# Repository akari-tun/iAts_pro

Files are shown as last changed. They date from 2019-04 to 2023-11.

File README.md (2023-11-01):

# iAts_pro(Antenna automatic tracking system pro)

## AAT test video
You can see the test video at [here](https://www.bilibili.com/video/av53142016).

## Development is on the way...

Not long ago, I created an automatic tracking system that supports bluetooth connection and parameter configuration based on the open source project [amv-open360tracker](https://github.com/raul-ortega/amv-open360tracker/) (You can find my project at [here](https://github.com/akari-tun/iAts)).

This project was built with Ateml 328p. As it is an 8-bit chip, its performance was low, so I couldn't implement more functions on it.Therefore, I came up with the idea of redeveloping it built on chips with higher performance.

Through the project of [RavenLRS](https://github.com/RavenLRS), I got to know a module espressif-ESP32 designed for IOT, which is integration bluetooth and wifi, and has 240mhz main frequency and 2m+ flash. And the official provides good SDK for development, which meets my needs very much. Therefore, I redeveloped the antenna automatic tracking system on this module.

After I graduating from college, I never use C language to develop any project, using C language development this project is a big challenge to me, I need to relearn C language feature, and the need to better understand how to use of Point. 

[RavenLRS](https://github.com/RavenLRS) project is built on ESP32 module, its also the realization of the function of some of its similar to some of my ideas, I learn by [RavenLRS](https://github.com/RavenLRS) project by learned a lot of of C language development experience, and use a lot of RavenLRS code to my project,Thanks to [RavenLRS](https://github.com/RavenLRS) author [fiam](https://github.com/fiam) open source for such an excellent project.

## How to Building iAts_pro
iAts_pro is built base on [esp-idf](https://github.com/espressif/esp-idf) v3.0 and has includes in path `/lib/esp-idf` as submodule, you need to install [Xtensa toolchanl](https://dl.espressif.com/dl/esp32_win32_msys2_environment_and_toolchain-20181001.zip) and set up the software environment follow the [ESP-IDF Programming Guide](https://docs.espressif.com/projects/esp-idf/en/v3.3/get-started/index.html).

Use command `git clone git@github.com:akari-tun/iAts_pro.git --recursive` to clone iAts_pro repository, `--recursive` option can clone all submoduls that includes, the submodul already points to the correct `Commit` from respository of `esp-idf` , do not need update it to lastest version.

Follow these command to build iAts_pro from your repository directory:

``` sh
cd iAts_pro
TARGET=esp32_iAts_pro_180 make
```

And you can add `PORT=<port>` and `flash` option to flash to your board like this:

``` sh
TARGET=esp32_iAts_pro_180 PORT=com1 make flash
```

## Companion App
I designed a android app for this project [Aircaft Viewer](https://github.com/akari-tun/iAts_pro/blob/master/tools).this app can be control aat to course the right direction and view the aircraft's location and some status infomation from the telemetry data.Its supported two protocol now.

## The Cases and STL file

[Body Build](https://github.com/akari-tun/iAts_pro/tree/master/doc/cases)

##### App Image

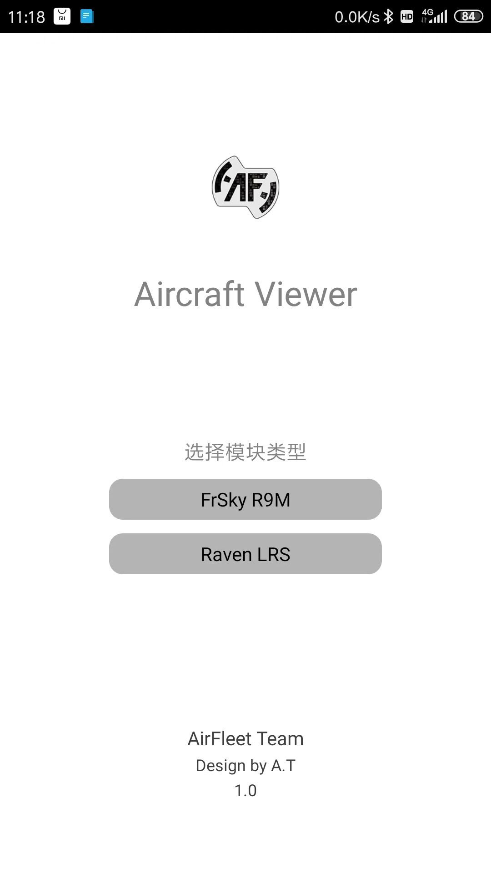
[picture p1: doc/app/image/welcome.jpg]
welcome


main page

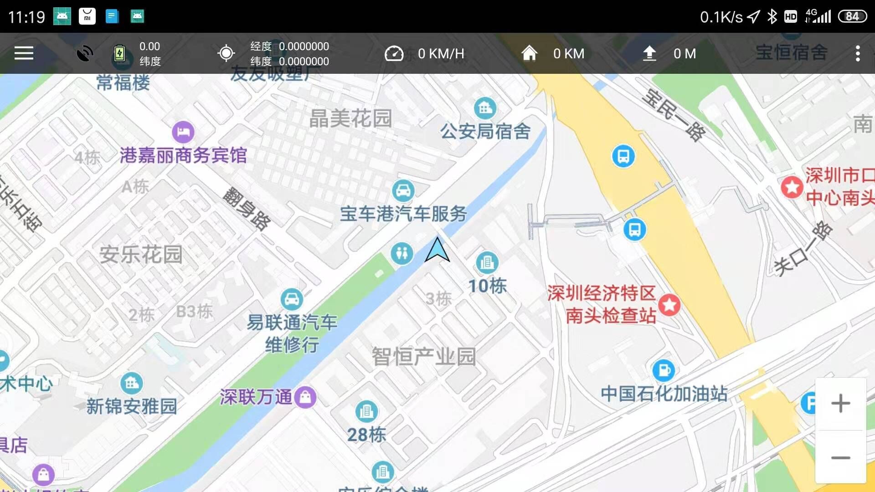
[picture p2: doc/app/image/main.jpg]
main

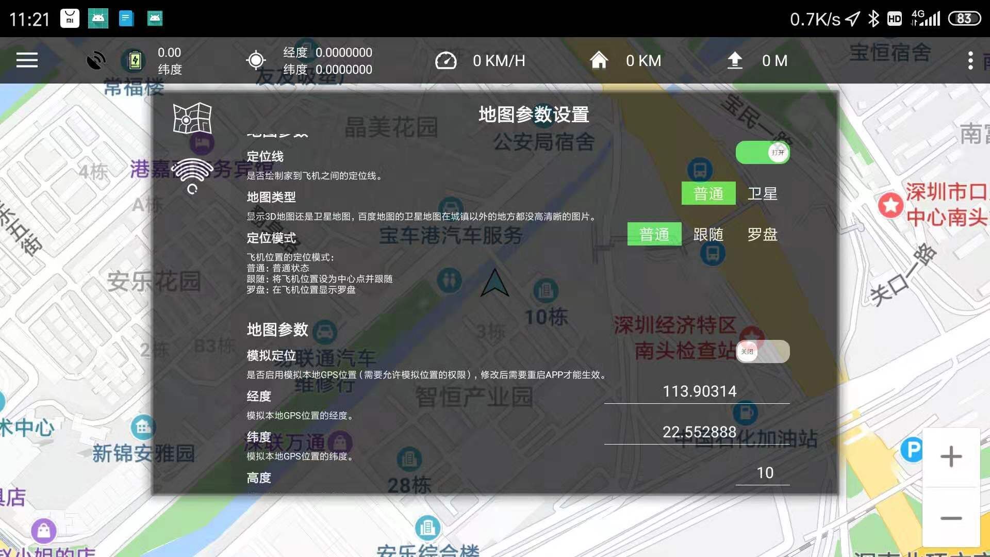
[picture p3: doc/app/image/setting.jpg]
setting


##### Smartport from R9M
Frsky R9m module can output Smartport, I diy a HC-05 module, It contains the inverter. So it's easy to plug to the R9m.

My app use classic bluetooth to connect HC-05 and get Smartport.

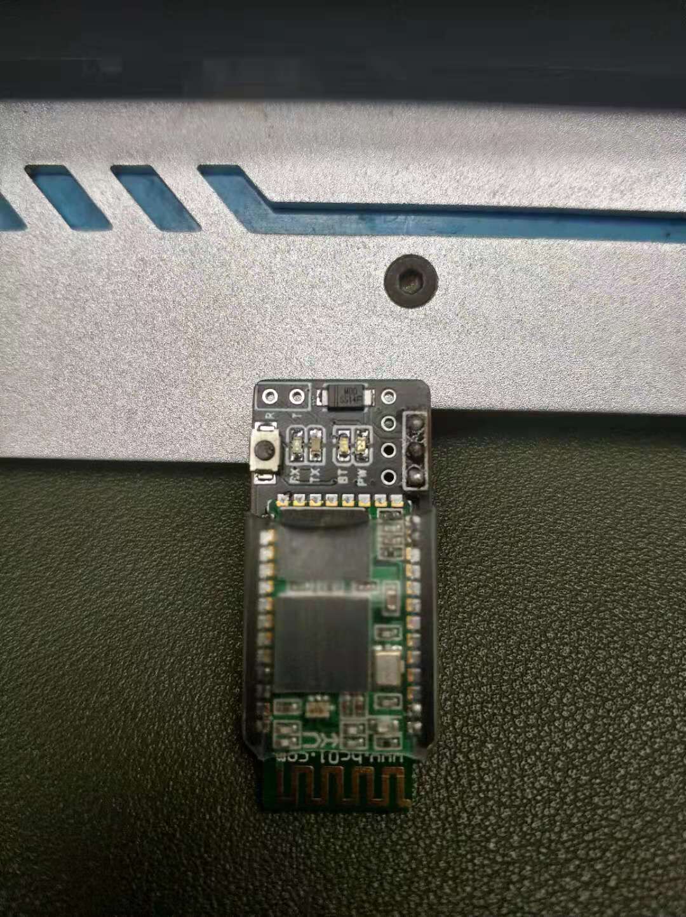
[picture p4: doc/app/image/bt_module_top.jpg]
bt_module_top

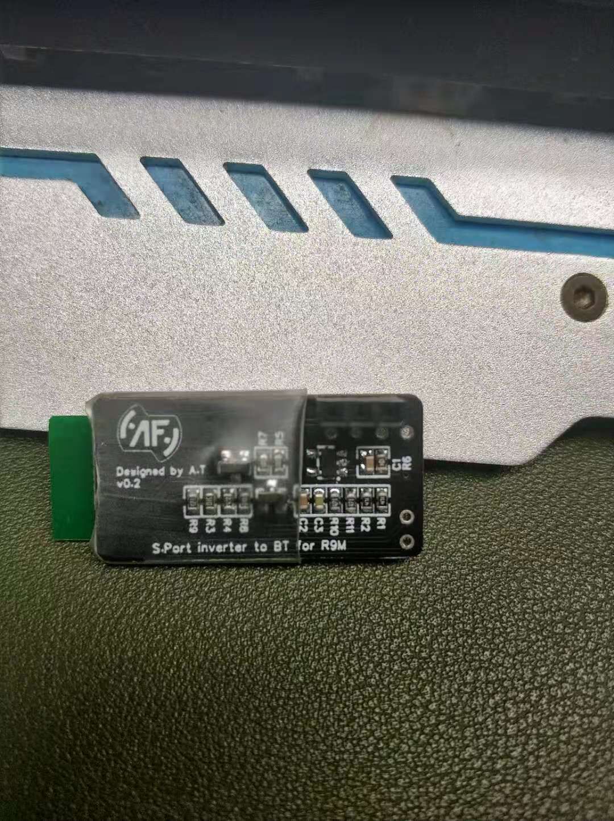
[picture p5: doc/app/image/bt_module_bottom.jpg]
bt_module_bottom


plugged to R9m

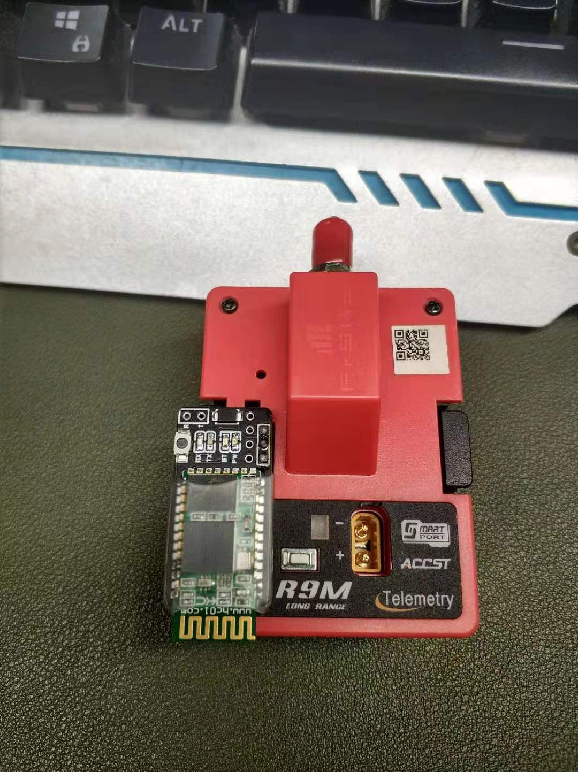
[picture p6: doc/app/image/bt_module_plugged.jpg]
bt_module_plugged


##### Raven LRS

[RavenLRS](https://github.com/RavenLRS) provides telemetry service for BLE's gatt server, but it don't provides notify.So I add the gatt server notify to RavenLRS,my app can use BLE notify get telemetry data.

You can find this module at here: [AF_TX_Lite](https://github.com/RavenLRS/raven-hardware/tree/AFelite)

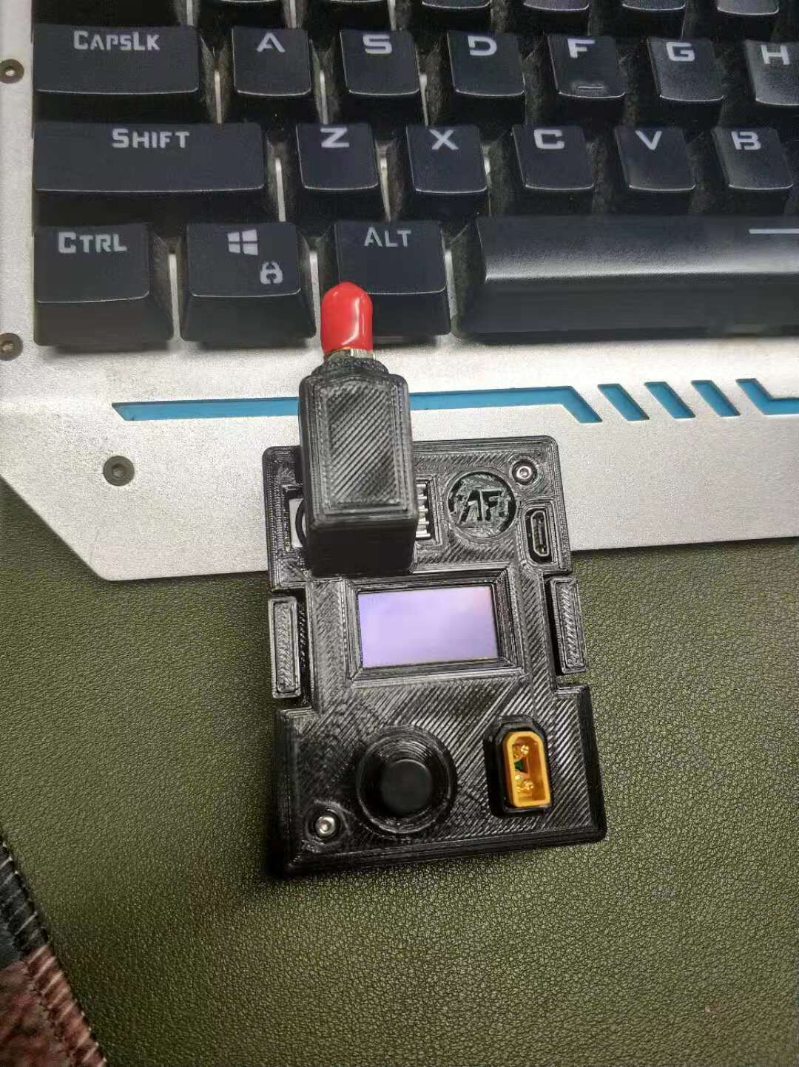
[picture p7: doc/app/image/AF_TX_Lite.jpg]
AF_TX_Lite


### PCB LAYOUT

#### PCB_LAYOUT_TOP
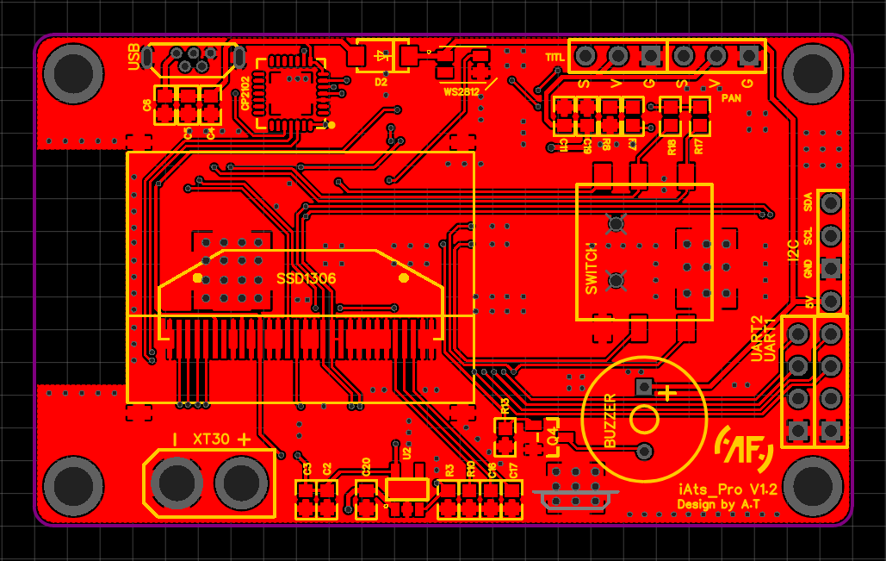
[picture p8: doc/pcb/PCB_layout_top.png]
PCB_LAYOUT_TOP


#### PCB_LAYOUT_BOTTOM
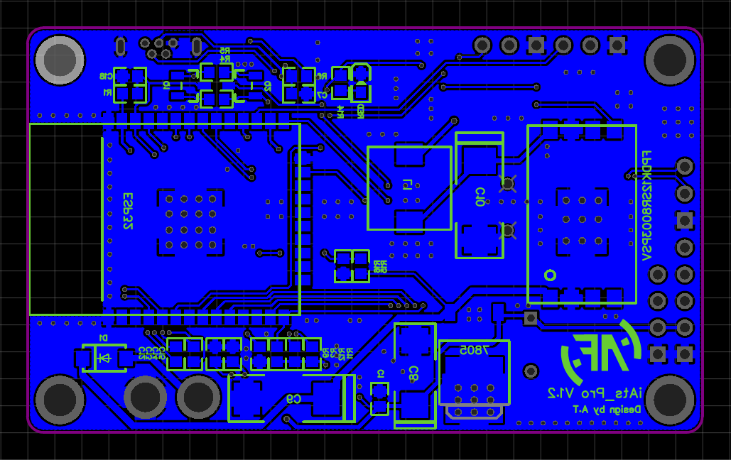
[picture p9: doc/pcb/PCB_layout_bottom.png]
PCB_LAYOUT_BOTTOM


### 3D PCB LAYOUT

#### 3D_PCB_LAYOUT_TOP
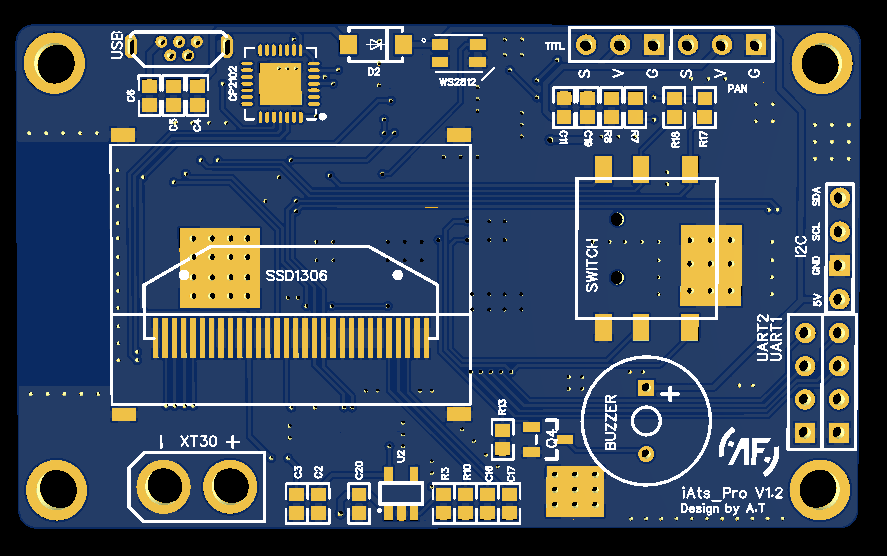
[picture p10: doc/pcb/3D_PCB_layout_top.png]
3D_PCB_LAYOUT_TOP


#### 3D_PCB_LAYOUT_BOTTOM
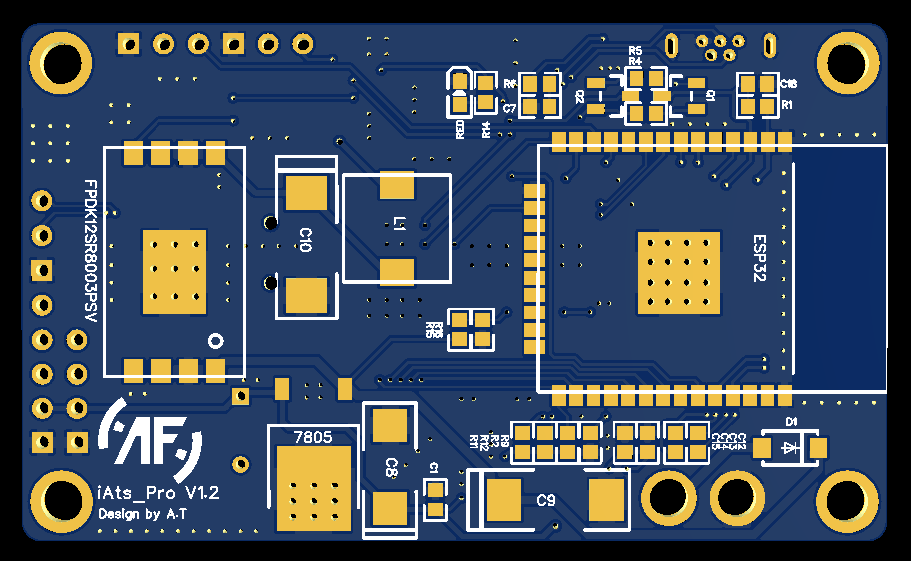
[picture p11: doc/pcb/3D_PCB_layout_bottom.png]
3D_PCB_LAYOUT_BOTTOM


### DESIGN IMAGE

#### 3D Printed
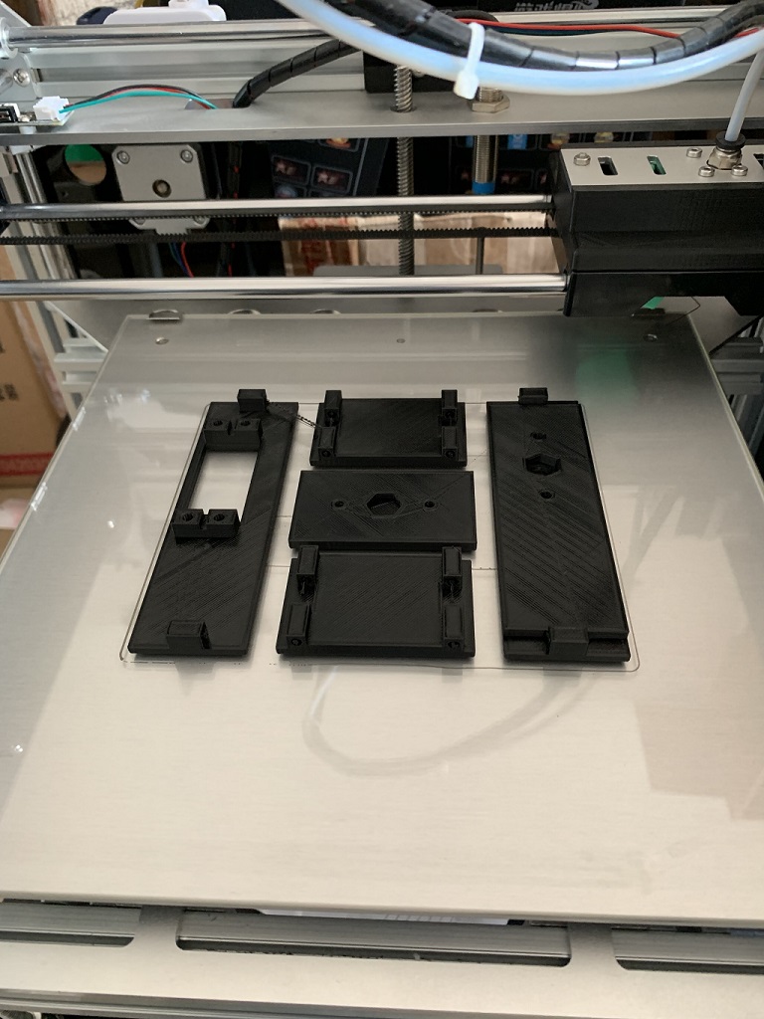
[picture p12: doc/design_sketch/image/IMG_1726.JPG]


#### Setup 1
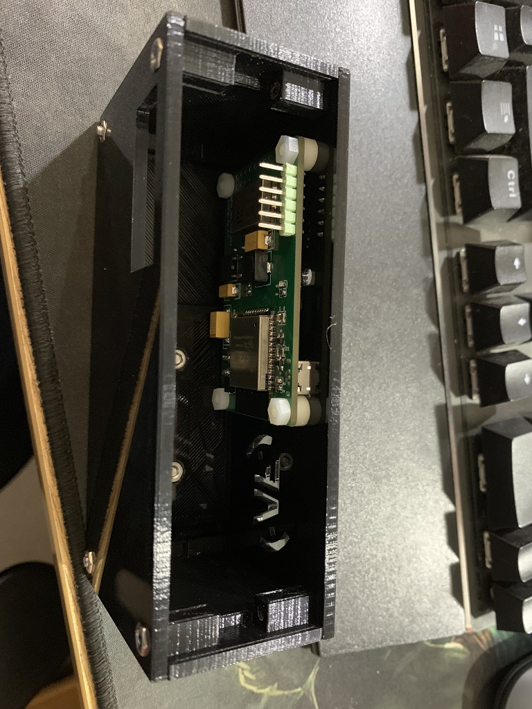
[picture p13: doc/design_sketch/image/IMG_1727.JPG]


#### Setup 2
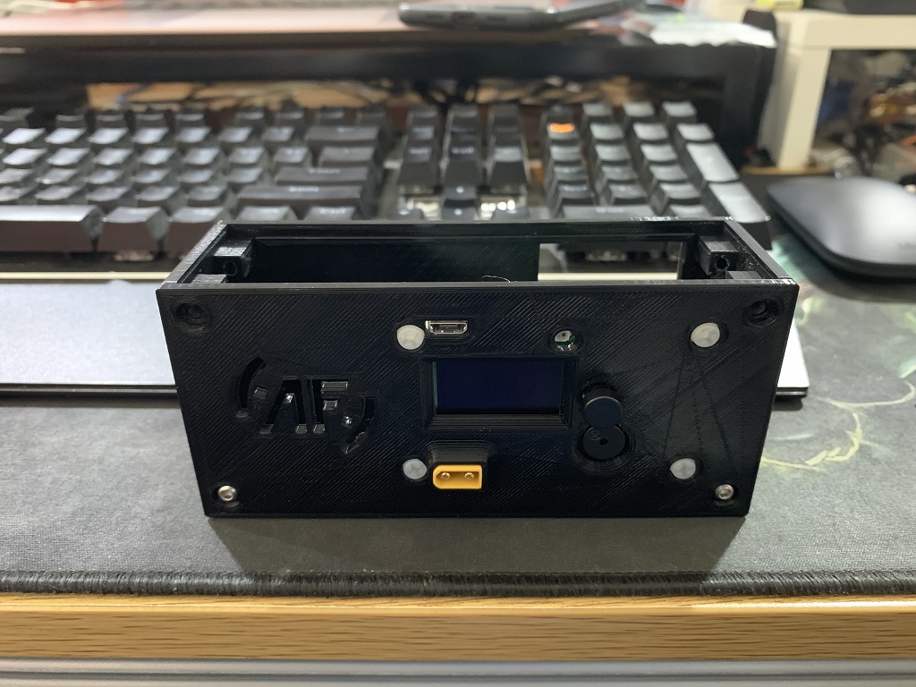
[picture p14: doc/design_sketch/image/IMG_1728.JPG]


#### Setup 3
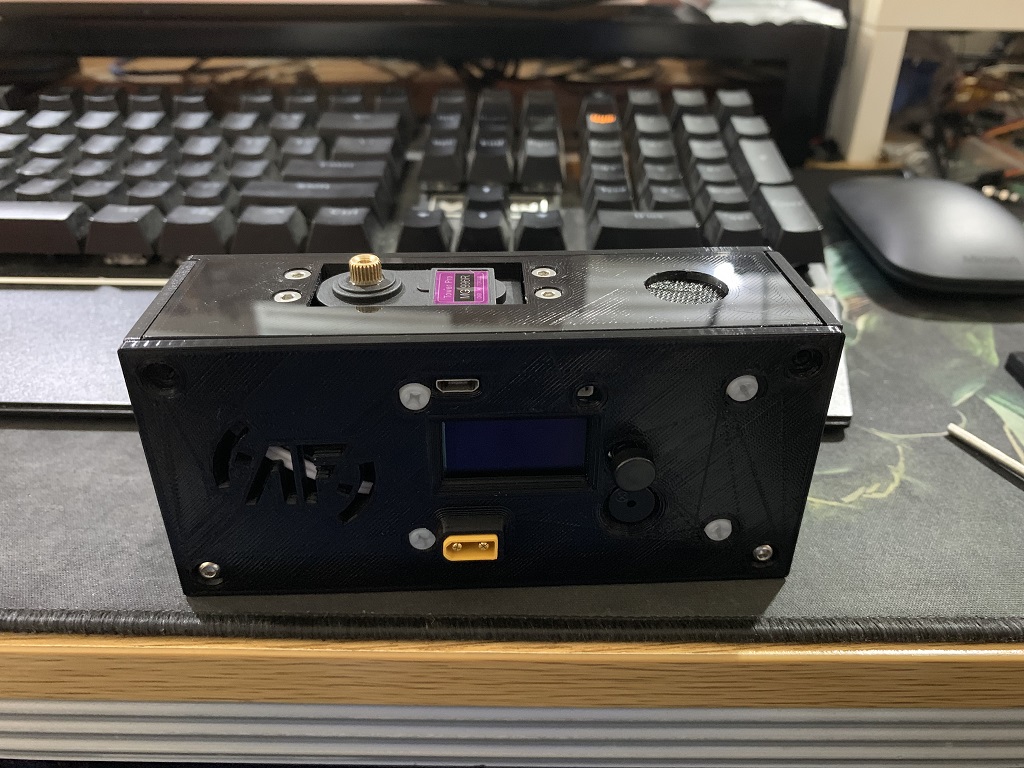
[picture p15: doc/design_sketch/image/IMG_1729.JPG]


#### Setup 4
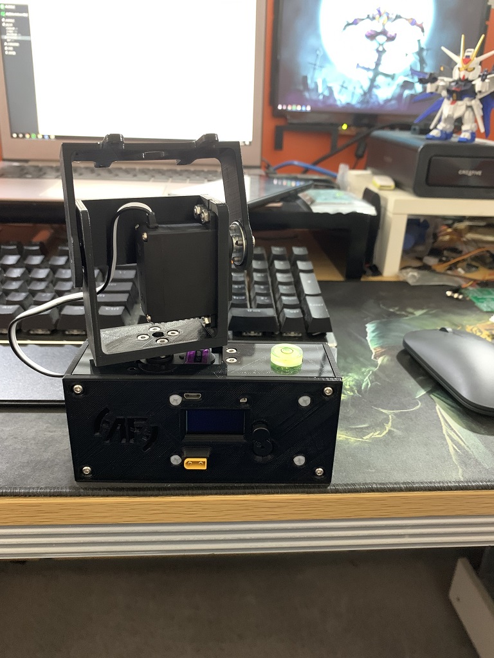
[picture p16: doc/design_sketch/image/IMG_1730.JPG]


#### Setup 5
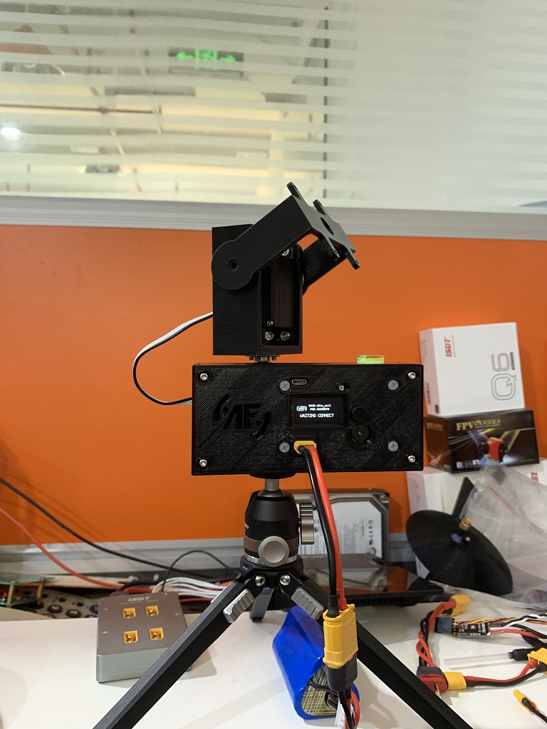
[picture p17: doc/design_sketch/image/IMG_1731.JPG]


#### Setup 6
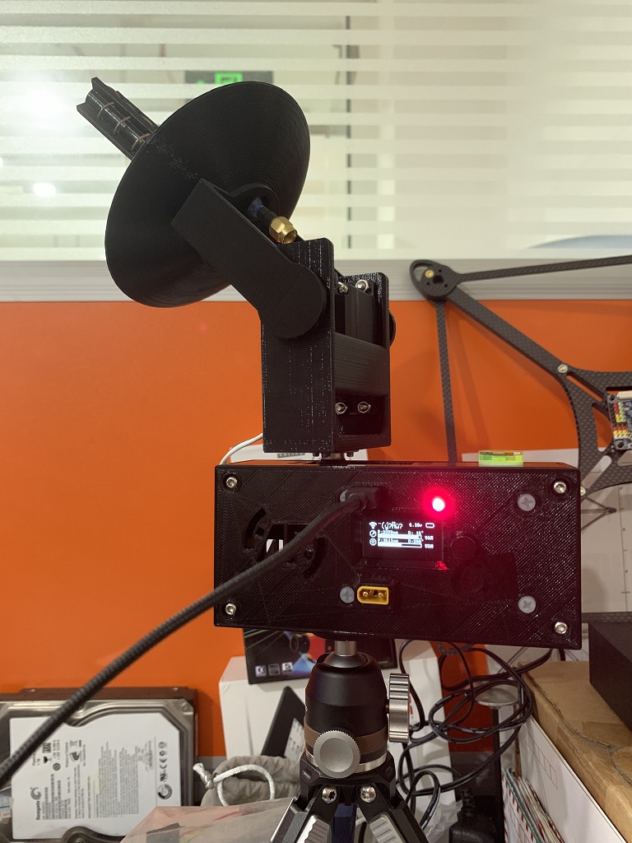
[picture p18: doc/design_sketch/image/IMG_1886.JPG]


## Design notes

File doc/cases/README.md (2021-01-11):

### Body
I provide STL files that can be sliced, and STP files that can be modified, so that you can modify the shell according to your own requirements.

### Print parameter
I use PLA filament to print this cases, 0.2mm resolution and 50% infill, at 1mm wall it has more strength, use 40mm/s speed for higher print quality.

### Attachment list
8  X M3 * 16 [screw](https://detail.tmall.com/item.htm?id=15880165683) for front and back panel  
4  X M3 * 12 [screw](https://detail.tmall.com/item.htm?id=15880165683) for pan servo  
2  X M3 * 10 [screw](https://detail.tmall.com/item.htm?id=15880165683) for 1/4 inch nut  
4  X M3 * 8  [screw](https://detail.tmall.com/item.htm?id=15880165683) for tilt servo  
10 X M3 [nut](https://detail.tmall.com/item.htm?id=20955552239&skuId=4319440520071) for servo  
1  X M3 * 10 [hand screw](https://detail.tmall.com/item.htm?id=17969634781&skuId=27553086583) for tilt stand  
8  X M3 * 6 [screw](https://detail.tmall.com/item.htm?id=15880165683) for steering wheel  
4  X M3 * 5 [nylon screw](https://detail.tmall.com/item.htm?id=17937568105&skuId=35998198392) for main board   
2  X 25T [steering wheel](https://item.taobao.com/item.htm?id=610941541573)  
1  X 1/4 inch [nut](https://detail.tmall.com/item.htm?id=22539384837&skuId=4297171597003)  
1  X 15 * 6 [level vial](https://item.taobao.com/item.htm?id=525788874394)  
1  X MF128zz [bearing](https://detail.tmall.com/item.htm?id=593627759602&skuId=4095252424985)  

#### Use Countersunk Screw

[Countersunk Screw](https://github.com/akari-tun/iAts_pro/tree/master/doc/cases/Countersunk%20Screw)

### Servo
I use the standard size of the servo, but the sizes of each servo different. I adjusted the design for sizes of the servo, and I recommend the use of this servo.  
[Pan servo](https://item.taobao.com/item.htm?id=581039145230&_u=b1i80m591e6) 180° 25kg digital servo  
[Tilt servo](https://item.taobao.com/item.htm?id=583942389297&_u=b1i80m530e0) 180° 12kg short digital servo

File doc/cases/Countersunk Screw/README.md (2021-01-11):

### Attachment list
8  X M3 * 16 [countersunk screw](https://detail.tmall.com/item.htm?id=19815788248&skuId=24958167102) for front and back panel  
4  X M3 * 12 [countersunk screw](https://detail.tmall.com/item.htm?id=19815788248&skuId=24958167101) for pan servo  
2  X M3 * 10 [countersunk screw](https://detail.tmall.com/item.htm?id=19815788248&skuId=24958167100) for 1/4 inch nut

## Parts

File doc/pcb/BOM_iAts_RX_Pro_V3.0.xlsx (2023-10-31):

iAts_Pro V3.0
元件 | 位置 | 规格 | 数量
电阻
47Ω | R8 | R0603 | 1
100Ω | R21 | R0603 | 1
470Ω | R20 | R0603 | 1
620Ω | R19,R18,R7 | R0603 | 3
1K | R25,R15 | R0603 | 2
4.7K | R11,R9,R29,R28,R12,R6 | R0603 | 6
5.76K | R24 | R0603 | 1
10K | R17,R16,R26,R27,R13,R14 | R0603 | 6
12K | R1,R5,R2,R4 | R0603 | 4
30.9K | R23 | R0603 | 1
100K | R22,R3 | R0603 | 2
910K | R10 | R0603 | 1
电容
1nF | C8 | C0603 | 1
100nF | C18,C4,C7,C5,C22,C11,C21 | C0603 | 7
1uF | C15,C10,C12,C2,C14,C1,C13 | C0603 | 7
2.2uF | C17 | C0603 | 1
4.7uF | C16 | C0603 | 1
10uF | C9,C3,C6 | C0603 | 3
22uF | C24,C23 | C0603 | 2
22uF | C27,C25,C19,C26,C20 | C0805 | 5
电感
4.7uH | L2 | IND-SMD_L4.0-W4.0 | 1
二极管
SS14 | D2 | SMA_L4.3-W2.6-LS5.2-RD | 1
SS34 | D1 | SMA_L4.4-W2.8-LS5.4-RD | 1
三极管
S8050 | Q4,Q3,Q2,Q1 | SOT-23-3_L3.0-W1.7-P0.95-LS2.9-BR | 4
LED
KT-0603R | G,B,R,Y | LED0603-R-RD | 4
WS2812B-3528 | WS2812 | LED-3528_4P | 1
IC
SX2106S6CTR | SX2106 | SOT-23-6_L2.9-W1.6-P0.95-LS2.8-BL | 1
SSD1306 | SSD1306 | SSD1306-30PIN_JX_REVERSE | 1
FPDK12SR8003PSV | FPDK12SR8003PSV | FPDK12SR8003PSV | 1
ESP-WROOM-32 | ESP32 | WIFIM-SMD_ESP-WROOM-32 | 1
CP2102-GMR | CP2102 | QFN-28_L5.0-W5.0-P0.50-BL-EP | 1
RT9013-33GB | U2 | SOT-23-5_L3.0-W1.7-P0.95-LS2.8-BL | 1
其他
Micro Usb 180 | USB | MICRO USB 180 | 1
ZL-DCY09605-2705P-5 | BUZZER | BUZ-TH_BD9.6-P5.00-D0.7-FD | 1
5Way Switch | SWITCH | 5WAY SWITCH | 1
XT30 | XT30 | XT30UPB_MY | 1

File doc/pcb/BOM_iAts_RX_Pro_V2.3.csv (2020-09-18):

ID | Name | Designator | Footprint | Quantity | Manufacturer Part | Manufacturer | Supplier | Supplier Part | LCSC Assembly
1 | WS2812B-3528 | WS2812 | LED-3528_4P | 1 | WS2812B-3528 | Worldsemi
2 | 4.7K | R12,R9,R29,R28,R11,R6 | R0603 | 6 | 0603WAF4701T5E | UniOhm | LCSC | C23162 | Yes
3 | 620 | R18,R19 | R0603 | 2 | 0603WAJ0621T5E | UniOhm | LCSC | C25251
4 | 100uF | C9 | CAP-SMD_L7.3-W4.3-R-RD | 1 | TAJE107K020RNJ | AVX | LCSC | C78063 | Yes
5 | 470uF | C10 | CAP-SMD_L7.3-W4.3-R-RD | 1 | TAJE477K010RNJ | AVX | LCSC | C7234 | Yes
6 | 10uF | C19,C6,C3 | C0603 | 3 | CL10A106KP8NNNC | SAMSUNG | LCSC | C19702 | Yes
7 | 4.7uF | C16 | C0603 | 1 | CL10A475KO8NNNC | SAMSUNG | LCSC | C19666 | Yes
8 | 30.9K | R23 | R0603 | 1 | 0603WAF3092T5E | UniOhm | LCSC | C23022 | Yes
9 | 3PIN_SERVO_2.54 | TITL,PAN | 3PIN_SERVO_2.54 | 2 | ?
10 | 100K | R3,R22 | R0603 | 2 | 0603WAF1003T5E | UniOhm | LCSC | C25803 | Yes
11 | 4.7uH | L2 | IND-SMD_L4.0-W4.0 | 1 | NR4018T4R7M | Taiyo Yuden | LCSC | C92936
12 | SS14 | D2 | SMA_L4.3-W2.6-LS5.2-RD | 1 | SS14 | STARSEA | LCSC | C84343 | Yes
13 | XT30_MY | XT30 | XT30UPB_MY | 1
14 | 5Way Switch | SWITCH | 5WAY SWITCH | 1 | TS-007 h:9 Five directions | ReliaPro | LCSC | C3679
15 | 2.2uF | C17 | C0603 | 1 | CL10A225KO8NNNC | SAMSUNG | LCSC | C23630 | Yes
16 | SX2106S6CTR | SX2106 | SOT-23-6_L2.9-W1.6-P0.95-LS2.8-BL | 1 | SX2106S6CTR | SX | LCSC | C78161 | Yes
17 | 5.76K | R24 | R0603 | 1 | 0603WAF5761T5E | UniOhm | LCSC | C23070 | Yes
18 | 100uF | C8 | CAP-SMD_L3.5-W2.8-R-RD | 1 | TCJB107M006R0070 | AVX | LCSC | C8026 | Yes
19 | 100nF | C18,C7,C4,C5 | C0603 | 4 | CC0603KRX7R9BB104 | YAGEO | LCSC | C14663 | Yes
20 | 620Ω | R7 | R0603 | 1 | 0603WAF6200T5E | UniOhm | LCSC | C23220 | Yes
21 | RT9013-33GB | U2 | SOT-23-5_L3.0-W1.7-P0.95-LS2.8-BL | 1 | RT9013-33GB | RICHTEK | LCSC | C47773 | Yes
22 | 100 | R21 | R0603 | 1 | 0603WAF1000T5E | UniOhm | LCSC | C22775 | Yes
23 | 4PIN | UART2,UART1 | 2.5-4PIN | 2 | ?
24 | 1K | R15,R25 | R0603 | 2 | 0603WAF1001T5E | UniOhm | LCSC | C21190 | Yes
25 | 1uF | C13,C14,C1,C15,C12,C2 | C0603 | 6 | CL10A105KB8NNNC | SAMSUNG | LCSC | C15849 | Yes
26 | KT-0603R | R,G,B,G2 | LED0603-R-RD | 4 | KT-0603R | KENTO | LCSC | C2286 | Yes
27 | 10K | R16,R17 | R0603 | 2 | TC0325F1002T5E | UniOhm | LCSC | C128781 | Yes
28 | CP2102-GMR | CP2102 | QFN-28_L5.0-W5.0-P0.50-BL-EP | 1 | CP2102-GMR | SILICON LABS | LCSC | C6568 | Yes
29 | SS34 | D1 | SMA_L4.4-W2.8-LS5.4-RD | 1 | SS34 | STARSEA | LCSC | C83961 | Yes
30 | S8050 | Q1,Q4,Q3,Q2 | SOT-23-3_L3.0-W1.7-P0.95-LS2.9-BR | 4 | S8050 | CJ | LCSC | C2146 | Yes
31 | 100nF | C11,C20,C21 | C0603 | 3 | CL10B104JB8NNNC | SAMSUNG | LCSC | C24452 | Yes
32 | 4PIN_I2C | I2C | 4PIN_I2C | 1 | ? |  |  | undefined
33 | ZL-DCY09605-2705P-5 | BUZZER | BUZ-TH_BD9.6-P5.00-D0.7-FD | 1 | ZL-DCY09605-2705P-5 | ZLFY | LCSC | C194534
34 | 470 | R20 | R0603 | 1 | 0603WAF4700T5E | UniOhm | LCSC | C23179 | Yes
35 | 910K | R10 | R0603 | 1 | RC0603FR-07910KL | YAGEO | LCSC | C137672
36 | 12K | R4,R5,R1,R2 | R0603 | 4 | 0603WAF1202T5E | UniOhm | LCSC | C22790 | Yes
37 | SSD1306 | SSD1306 | SSD1306-30PIN_JX_REVERSE | 1
38 | 33uH | L1 | IND-SMD_L7.8-W7.8 | 1 | SWRH0704B-330MT | Sunlord | LCSC | C127735
39 | 47Ω | R8 | R0603 | 1 | 0603WAF470JT5E | UniOhm | LCSC | C23182 | Yes
40 | 10 | R27,R26,R13,R14 | R0603 | 4 | 0603WAF100JT5E | UniOhm | LCSC | C22859 | Yes
41 | Micro Usb 180 | USB | MICRO USB 180 | 1
42 | ESP-WROOM-32 | ESP32 | WIFIM-SMD_ESP-WROOM-32 | 1 | ESP-WROOM-32 | ESPRESSIF | LCSC | C95209
43 | FPDK12SR8003PSV | FPDK12SR8003PSV | FPDK12SR8003PSV | 1 | FPDK12SR8003PSV |  | FDK | undefined
44 | 2PIN | UART0 | 2PIN | 1 | ?

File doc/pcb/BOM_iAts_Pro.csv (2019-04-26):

ID | Name | Designator | Footprint | Quantity | Manufacturer Part
1 | CP2102-GMR | CP2102 | QFN-28_5X5X05P | 1 | CP2102-GMR
2 | 100nF | C4,C5,C7,C18 | 0603' | 4 | CC0603KRX7R9BB104
3 | 10uF | C6,C19,C20,C3 | 0603' | 4 | CL10A106KP8NNNC
4 | 4.7K | R6,R11,R12,R17,R18,R9 | 0603' | 6 | 0603WAF4701T5E
5 | S8050 | Q1,Q2,Q4 | SOT-23(SOT-23-3) | 3 | S8050
6 | 12K | R4,R5,R1,R2 | 0603' | 4 | 0603WAF1202T5E
7 | Micro Usb 180 | USB | MICRO USB 180 | 1 | ?
8 | 470uF | C9,C10 | CASE-E_7343 | 2 | TAJE477K010RNJ
9 | SS34 | D1 | SMA(DO-214AC) | 1 | SS34
10 | FPDK12SR8003PSV | FPDK12SR8003PSV | FPDK12SR8003PSV | 1 | FPDK12SR8003PSV
11 | 620Ω | R7 | 0603' | 1 | 0603WAF6200T5E
12 | 47Ω | R8 | 0603' | 1 | 0603WAF470JT5E
13 | 33uH | L1 | 0704' | 1 | SWRH0704B-330MT
14 | 100nF | C11 | 0603' | 1 | CL10B104JB8NNNC
15 | SS14 | D2 | SMA(DO-214AC) | 1 | SS14
16 | 7805 | 7805 | TO252 | 1 | ?
17 | 100uF | C8 | CASE-C_6032 | 1 | TAJC107K016RNJ
18 | 10 | R15,R13 | 0603' | 2 | 0603WAF100JT5E
19 | 1K | R16 | 0603' | 1 | 0603WAF1001T5E
20 | XT30_MY | XT30 | XT30UPB_MY | 1 | ?
21 | ESP-WROOM-32 | ESP32 | ESP-WROOM-32 | 1 | ESP-WROOM-32
22 | WS2812B-3528 | WS2812 | LED-3528_4P | 1 | WS2812B-3528
23 | 4PIN_I2C | I2C | 4PIN_I2C | 1 | ?
24 | 4PIN | UART1,UART2 | 2.5-4PIN | 2 | ?
25 | 3PIN_SERVO_2.54 | TITL,PAN | 3PIN_SERVO_2.54 | 2 | ?
26 | ZL-DCY09605-2705P-5 | BUZZER | BUZZER-R9.6-2P-5.0PITCH | 1 | ZL-DCY09605-2705P-5
27 | 5Way Switch | SWITCH | 5WAY SWITCH | 1 | TS-007 h:9 Five directions
28 | 0.96-OLED-30Pin_JX | SSD1306 | SSD1306-30PIN_JX | 1 | 0.96'OLED-30Pin
29 | 1uF | C12,C13,C14,C15,C1,C2 | 0603' | 6 | CL10A105KB8NNNC
30 | 4.7uF | C16 | 0603' | 1 | CL10A475KO8NNNC
31 | 2.2uF | C17 | 0603' | 1 | CL10A225KO8NNNC
32 | 910 | R10 | 0603' | 1 | 0603WAF910JT5E
33 | RT9013-33GB | U2 | SOT-23-5 | 1 | RT9013-33GB
34 | 100K | R3 | 0603' | 1 | 0603WAF1003T5E
35 | KT-0603R | RED | LED-0603 | 1 | KT-0603R
36 | 470 | R14 | 0603' | 1 | 0603WAF4700T5E

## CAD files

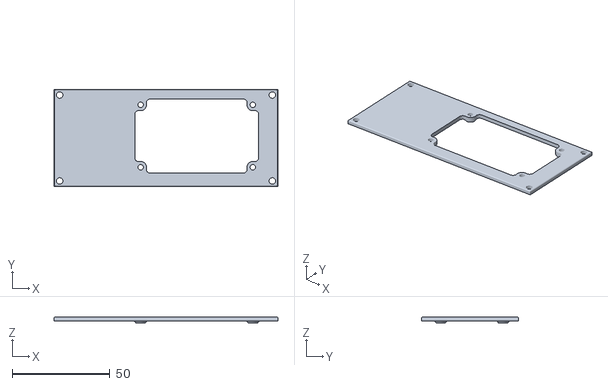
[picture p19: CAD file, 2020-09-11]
doc/cases/iAts_Pro_Mainboard_holder.stl
114.8 x 49.8 x 3.00

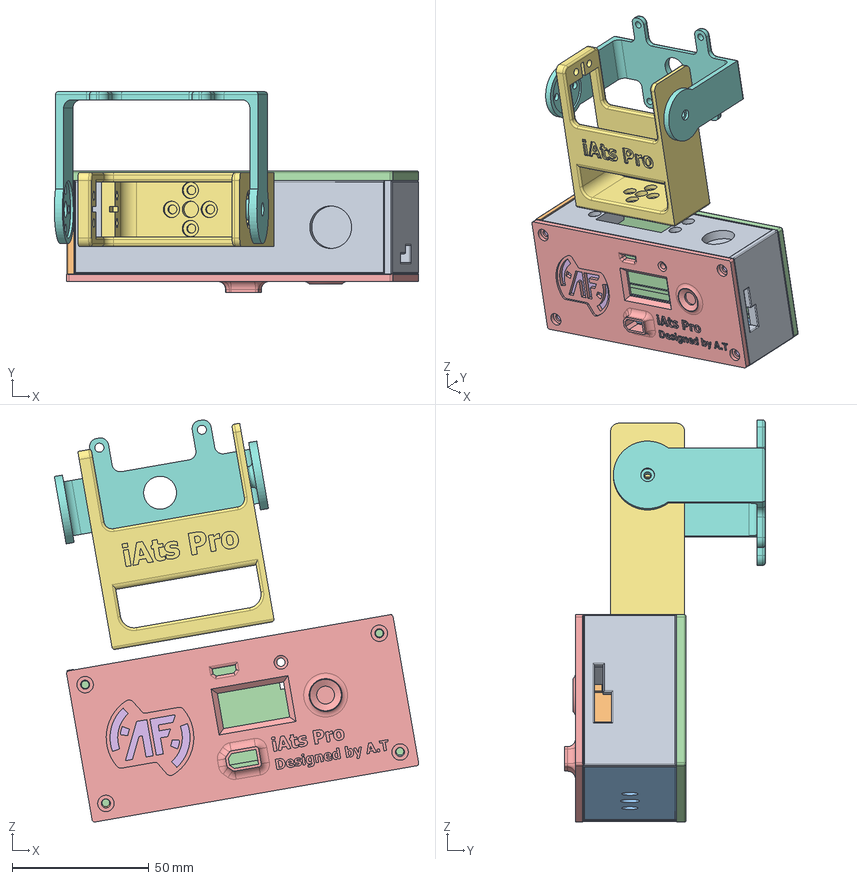
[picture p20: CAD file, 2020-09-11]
doc/cases/iAts_Pro_Cases.stp
133.0 x 73.3 x 146.7 mm
iAts_Pro_Pan_Servo_holder
iAts_Pro_Pan_Side_plate
iAts_Pro_Pan_Bottom
iAts_Pro_Back
iAts_Pro_Front_V3
iAts_Pro_Mainboard_holder
iAts_Pro_Tilt_servo_holder
天线支架
iAts_Pro_Pan_Side_plate_1

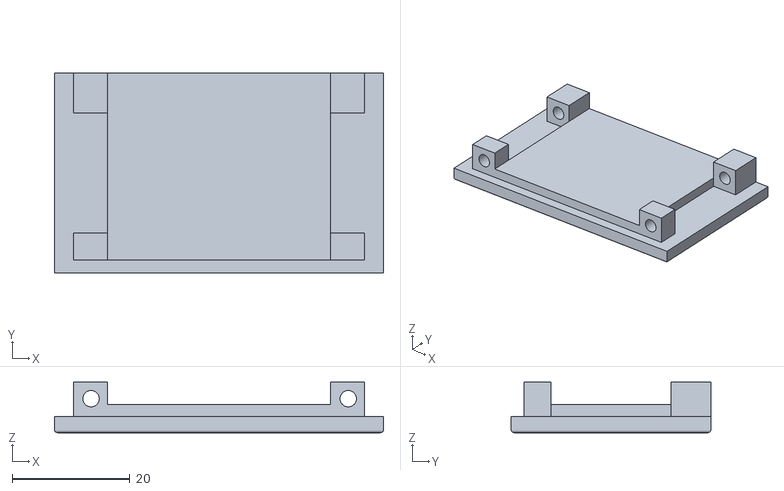
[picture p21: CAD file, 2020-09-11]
doc/cases/iAts_Pro_Side_Left_plate.stl
56.0 x 34.0 x 8.60

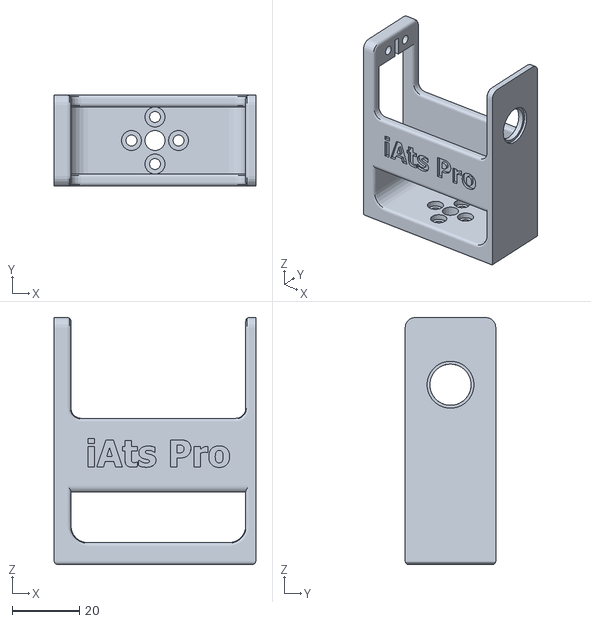
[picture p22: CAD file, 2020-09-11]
doc/cases/iAts_Pro_Tilt_servo_holder_L40.5.stl
60.0 x 27.0 x 73.5

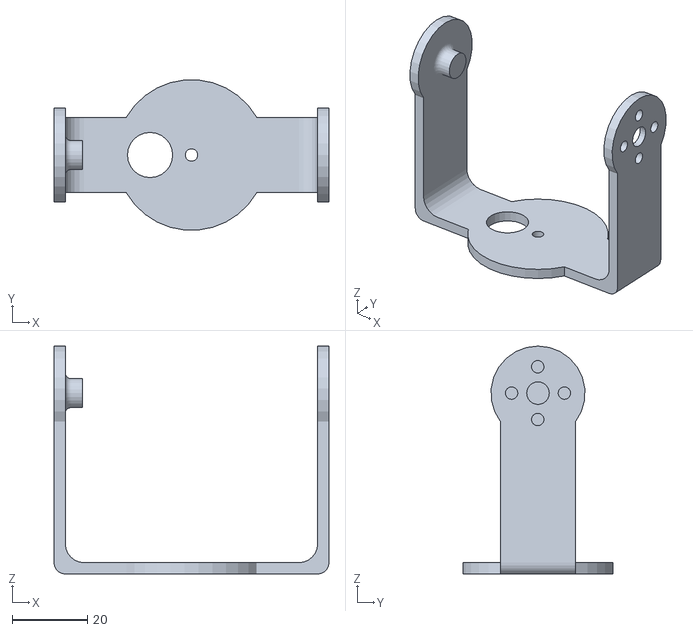
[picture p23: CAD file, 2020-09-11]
doc/cases/iAts_Pro_Helical_Antenna_short_servo_holder.stl
73.0 x 39.8 x 60.5

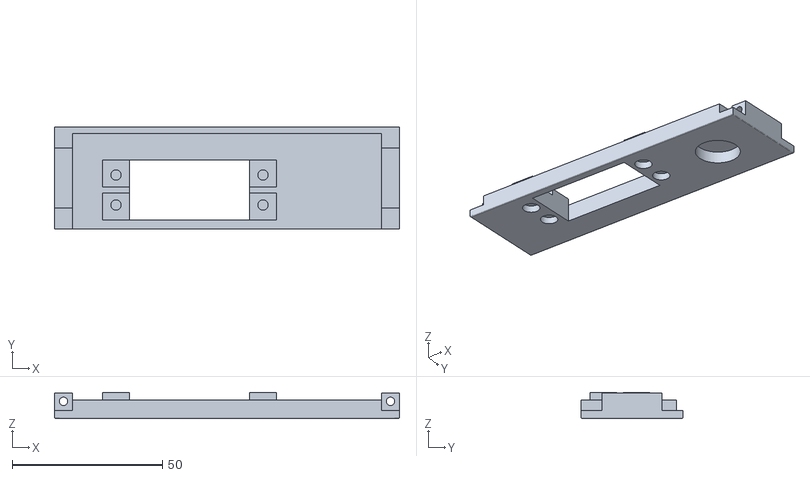
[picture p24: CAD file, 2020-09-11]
doc/cases/iAts_Pro_Pan_Servo_holder.stl
115.0 x 34.0 x 8.80

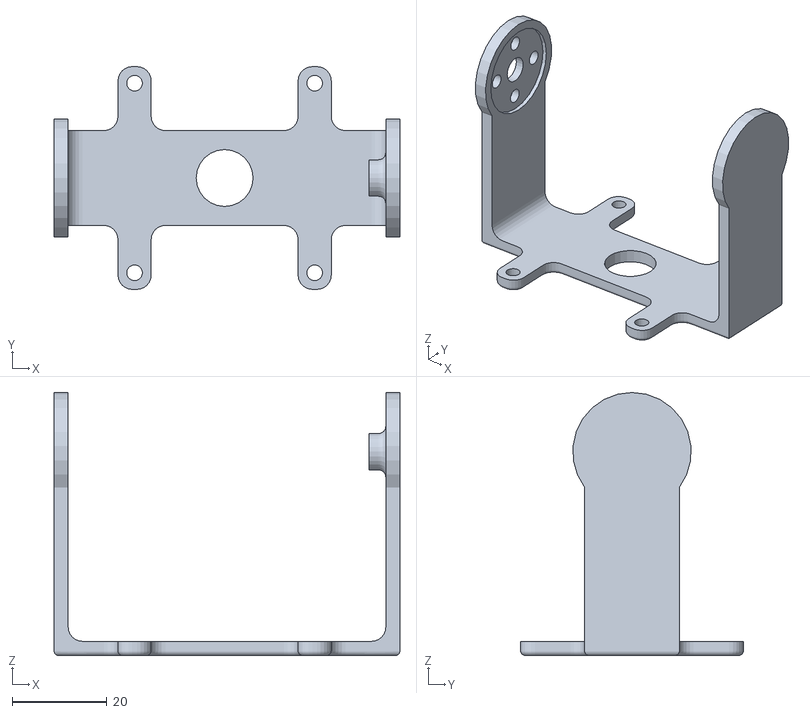
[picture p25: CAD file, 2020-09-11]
doc/cases/iAts_Pro_Antenna_short_servo_holder.stl
73.0 x 47.0 x 55.5

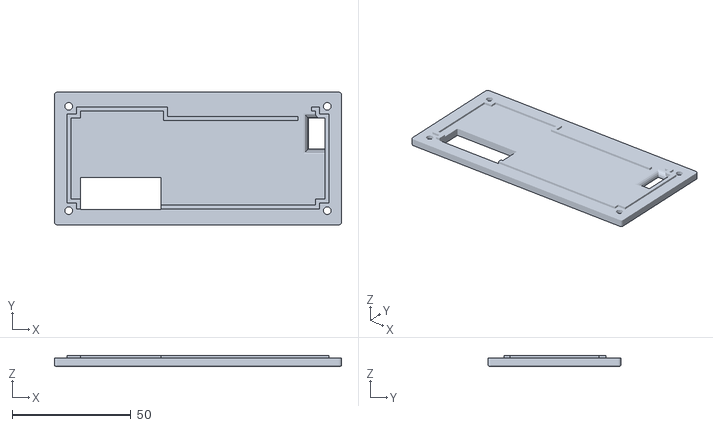
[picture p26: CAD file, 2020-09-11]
doc/cases/iAts_Pro_Back.stl
121.0 x 56.0 x 4.50

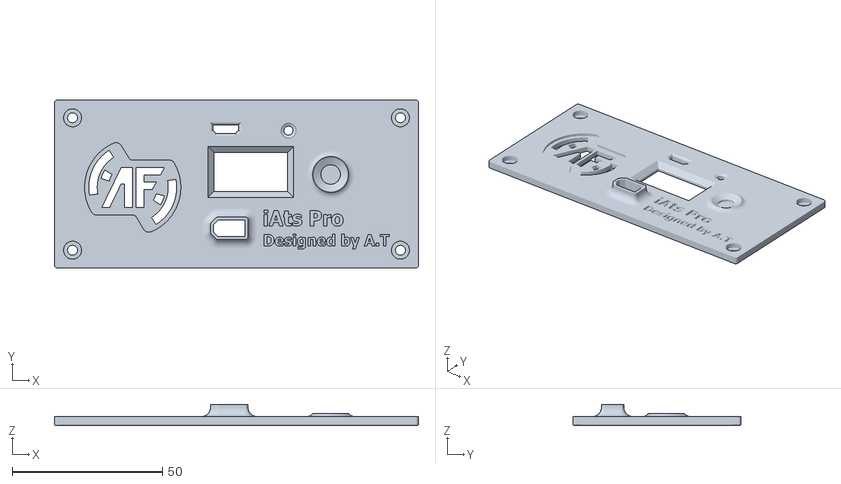
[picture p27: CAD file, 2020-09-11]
doc/cases/iAts_Pro_Front_V3.stl
121.0 x 56.0 x 7.00

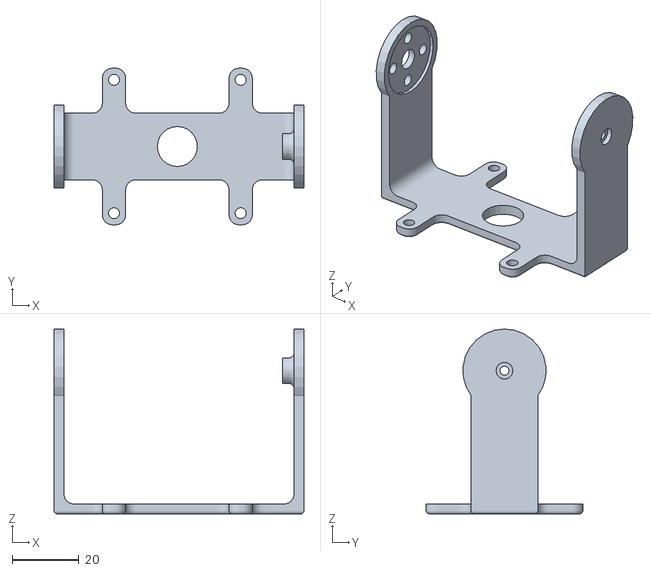
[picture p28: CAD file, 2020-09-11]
doc/cases/iAts_Pro_Antenna_holder.stl
75.0 x 47.0 x 55.5

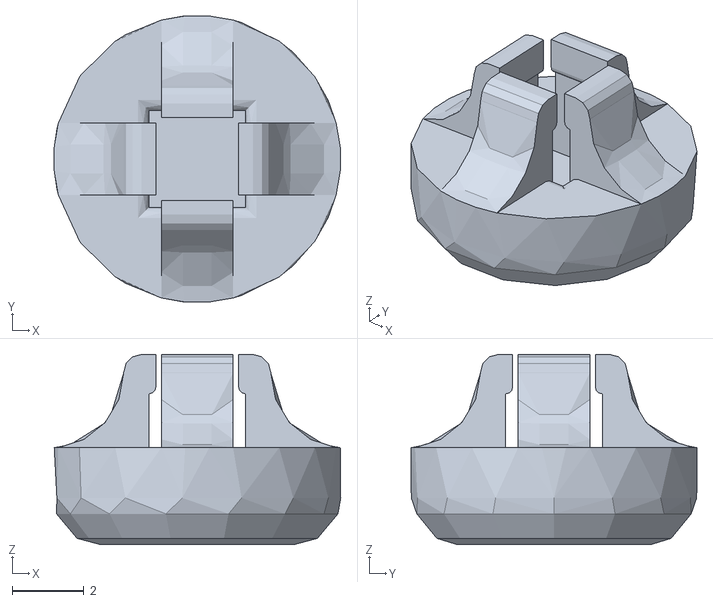
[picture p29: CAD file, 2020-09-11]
doc/cases/iAts_Pro_Switch_stick_cap.stl
7.99 x 7.97 x 5.30

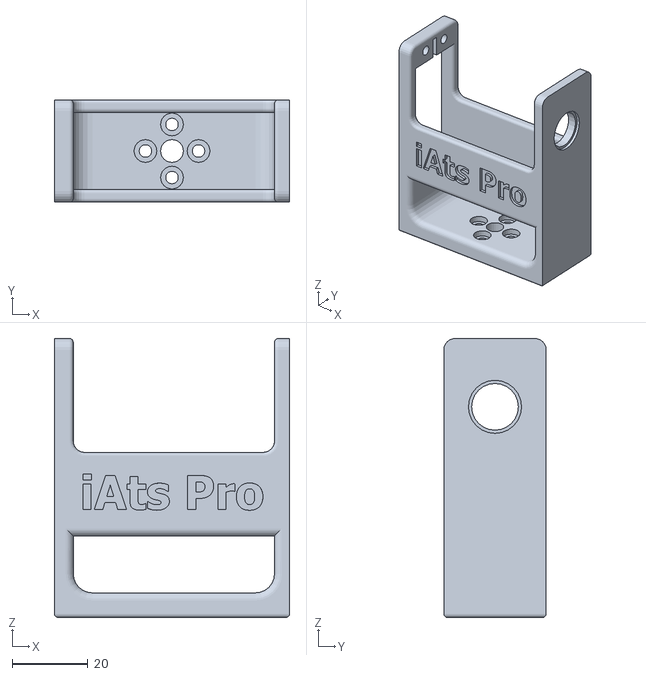
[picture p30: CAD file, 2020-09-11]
doc/cases/iAts_Pro_Tilt_short_servo_holder.stl
62.0 x 27.0 x 73.5

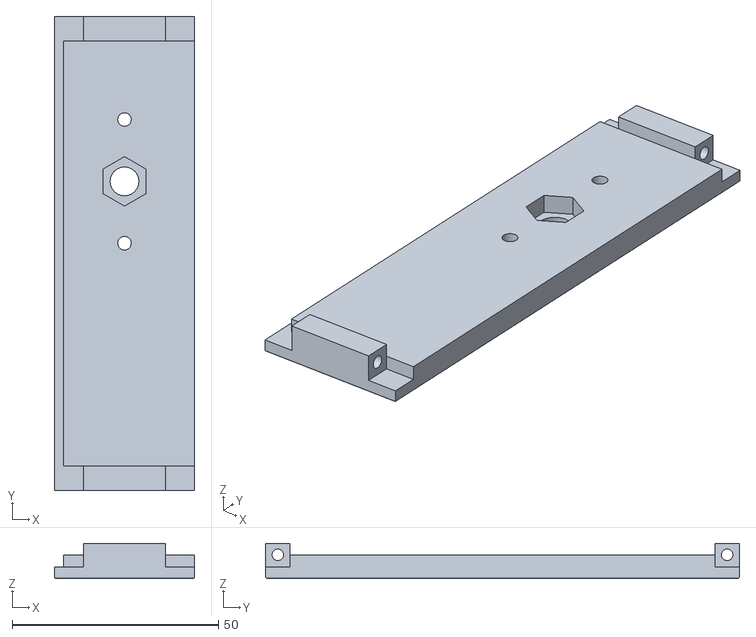
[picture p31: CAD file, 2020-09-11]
doc/cases/iAts_Pro_Bottom.stl
34.0 x 115.0 x 8.60

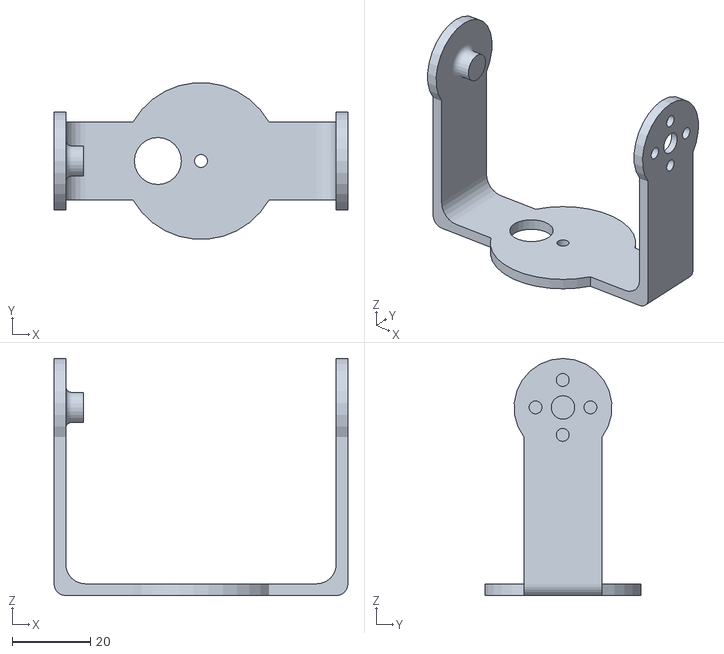
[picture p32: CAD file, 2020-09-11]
doc/cases/iAts_Pro_Helical_Antenna_holder.stl
75.0 x 39.8 x 60.5

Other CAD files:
doc/cases/iAts_Pro_Pan_Servo_holder_L40.5.stl
doc/cases/iAts_Pro_Side_Right_plate.stl
doc/cases/iAts_Pro_TFP_Antenna_holder.stl
doc/cases/iAts_Pro_Antenna_holder_20db_small.stl
doc/cases/Countersunk Screw/iAts_Pro_Back.stl
doc/cases/Countersunk Screw/iAts_Pro_Bottom.stl
doc/cases/Countersunk Screw/iAts_Pro_Front_V3.stl
doc/cases/Countersunk Screw/iAts_Pro_Pan_Servo_holder.stl
doc/cases/iAts_Pro_Nut_holder.stl
doc/cases/iAts_Pro_Tilt_servo_holder.stl

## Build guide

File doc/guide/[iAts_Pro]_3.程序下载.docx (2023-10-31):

下载程序

主板焊接完成后，首次需要通过电脑的USB口转TTL连接到板子的串口上进行程序的下载，以后也可以通过这种方式来升级程序，很快也会支持通过APP来进行空中升级。

接线：

USB连接到TTL有两个方式可以选择：

1. 焊接了CP2102芯片，直接插USB接口

主板上如果焊接了CP2102芯片，那么直接通过MicroUsb线连接到主板上的USB接口,如下图所示：

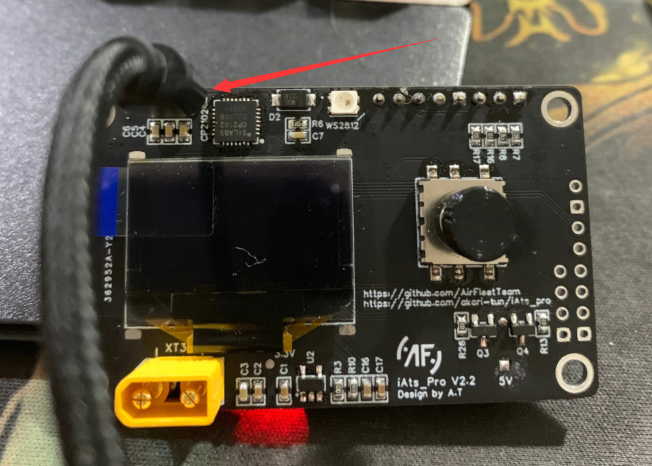
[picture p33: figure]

成功连接电脑后应该能看到正确的串口

2. 通过USB转TTL转接小板连接

将TTL转接小板的TX/RX分别连接到UART0的RX/TX：

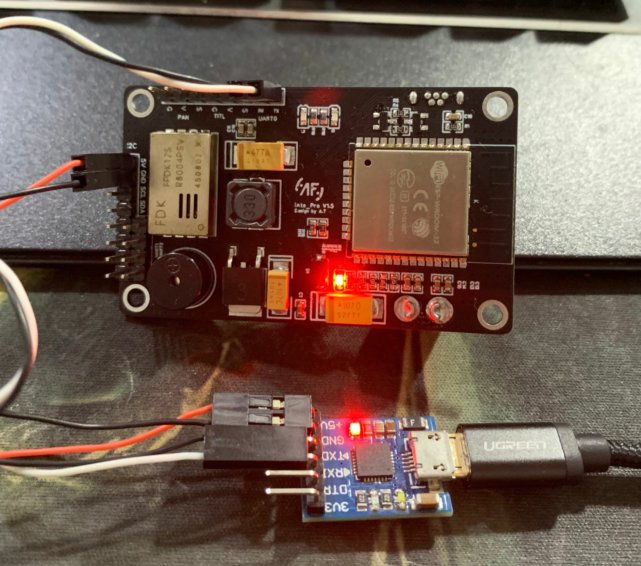
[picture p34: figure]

主板 小板

TX <------> RX

RX <------> TX

GND <-------> GND

5v <-------> 5v

下载工具：

本项目是基于ESP32芯片编写的，所以下载工具需要使用ESPFlashDownloadTool，

下载地址：

https://www.espressif.com/sites/default/files/tools/flash_download_tools_v3.6.6.zip

下载完成后运行程序：

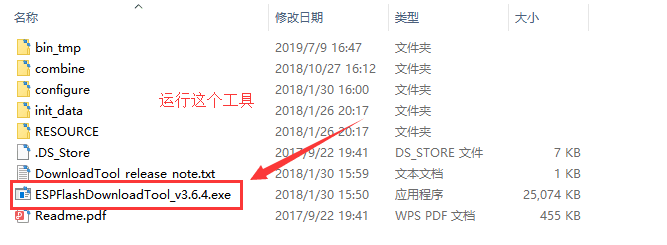
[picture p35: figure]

点击ESP32 DownloadTool 按钮进入程序下载界面：

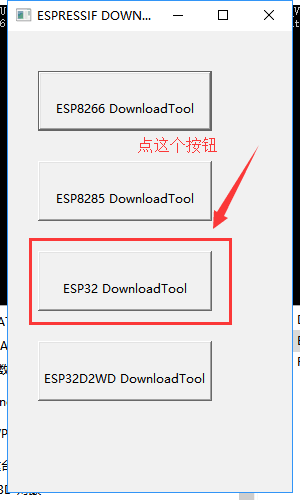
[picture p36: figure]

下载界面打开后，分别载入3个文件

bootloader.bin 芯片的引导程序，对应地址 0x1000

iAts_pro.bin 主程序，对应地址 0x10000

partitions.bin 分区配置，对应地址 0x8000

如下图:

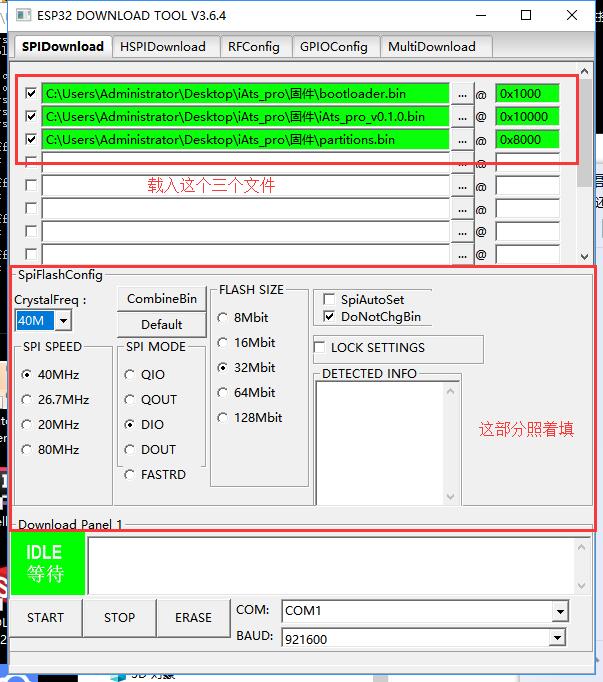
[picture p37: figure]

下载程序：

下载工具都配置好后，选择正确的串口与合适的波特率：

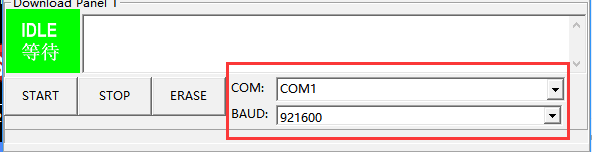
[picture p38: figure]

如果是第一下载程序或者是想清除数据恢复默认设置，那么可以点 ERASE 按钮先擦除数据。

点击 START 按钮即可开始下载程序，点击按钮之前，需要将板子复位并进入下载模式，有两种方式进入下载模式：

1. 板子本身设计有自复位电路，如果使用板载的USB口进行程序下载，那么板子会自动复位并进入下载模式。
2. 将板子断电，之后按住板子五向按键的“中键”并给板子上电，那么板子就会进入下载模式。

程序下载中

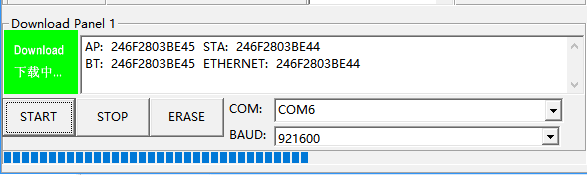
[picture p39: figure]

程序下载完成

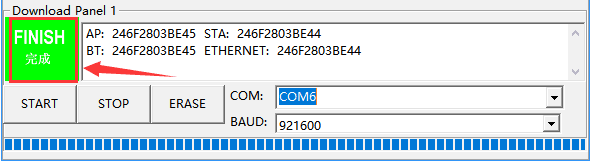
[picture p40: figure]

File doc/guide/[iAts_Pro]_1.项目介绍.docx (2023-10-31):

前言

不久之前（大概在2017年末），我在基于开源AAT项目amv-open360tracker (https://github.com/raul-ortega/amv-open360tracker/)（https://github.com/raul-ortega/amv-open360tracker/）开发了支持蓝牙连接手机APP功能的APP，可以通过手机APP方便的对AAT进行调参，并能在APP上显示一些简单的飞行数据。（项目地址：https://github.com/akari-tun/iAts）

由于这个项目是构建于8位的单片机Atmel 328p芯片上，其低下性能限制了我在其上实现更多功能的想法，所以我需要在更高性能的平台上重新开发一套AAT。

大概在去年年底，通过RavenLRS（https://github.com/RavenLRS/raven）项目了解到一款乐鑫

ESP32专门为IOT设计的开发板，它同时集成了WIFI与蓝牙，并且拥有双核240Mhz的主频率与2m+的flash容量。乐鑫官方为开发者提供了非常完善的SDK，其非常符合我的需求，所以我在今年的年后乘工作不太忙的时候在其上重新开发了全新的AAT程序，我将其命名为iAts_pro （Internet Automatic Tracking System Pro）其中Internet的来源本意是我在修改蓝牙版本的AAT时候，是希望通过AAT的蓝牙回传飞行器的坐标数据到手机APP，并通过APP将数据上传到云端，可以记录并回顾一些飞行数据（例如直接生成KML文件导入到GoogleEarth），就是类似现在物联网internet of things产品的设计思路，但是由于种种原因（主要是当时舍不得花钱买服务器，虽然后面买了便宜的云服务器，但是那个项目以后应该也不会维护了），这个功能尚未实现，但是名称我依然沿用下来了，后期应该会实现这些功能。

虽然在大学里学过C语言，但是自从大学毕业后从来没用C语言开发过项目，此项目的开发对于我来说是一个巨大的挑战，我必须重新进行C语言特性的学习。

因为RavenLRS也是基于ESP32开发的，并且它的一些功能与我的设想很像，所以通过RavenLRS的源码，我学习到了大量的C语言的经验，并在我的项目中使用了它的大量的代码。

RavenLRS的相关教程可以看管爷的帖子：

http://www.moz8.com/search.php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）

产品简介

iAts_pro是基于ESP32模块构建的一款天线自动跟踪系统，主要应用于航模FPV飞行时装载高增益定向天线，根据本地GPS坐标与飞行器的GPS坐标计算出相对方位角与高度角，并移动天线将天线指向飞行器，以接收到更强的信号。

在进行结构原型设计时，考虑了以下几点：

1. 结构简单，使用时下比较流行的双180度舵机的结构，这样运动部分结构非常轻便简洁，主要重量在舵机与天线，减少了水平方向运动的负荷。
2. 结构结实稳固，选用标准尺寸舵机，提供了足够的扭力，不会出现翻转天线时候导致整个云台的震动。
3. 方便拆卸，天线支架部分实现快拆，方便更换天线，运动部分与底部能实现快拆，方便收纳。
4. 方便安装，设计1/4英寸螺母，以便的安装到三脚架上。
5. 带有水平尺，方便固定在三脚架上的时候找平。
6. 结构需要能很方便的进行3D打印。

在功能设计部分，考虑了以下功能：

1. WIFI无线互联，手机开放WIFI热点，连接到WIFI后可以通过APP进行一些控制与调参等操作，并未以后的功能扩展留下无数的可能。
2. 带有屏幕，通过屏幕显示一些AAT当前的一些信息。
3. 方便操作，可以通过按键来进行一些简单的操作与设置。
4. 支持数传协议，支持目前流行的各种数传协议，例如MSP，SPort，MAVLink等等。
5. 固件升级方便，使用APP进行远程OTA升级。

在PCB设计时，考虑了以下几点：

1. 小体积，PCB大小在5cm*5cm左右，以便将结构设计得很小。
2. 双电源，ESP32与舵机分开供电，保证ESP32模块的供电稳定与舵机的供电充足。
3. 方便扩展，预留I2C接口与串口。
4. 调试升级方便，集成USB转TTL的CP2102芯片，可以直接通过MiniUsb接口连接电脑进行调试与下载固件。
5. 通用的接口，XT30公头，2.45mm排针。
6. 方便固定，四角M3螺丝固定孔。

主要特点

* 结构简单，主要的成本是两个标准舵机，并且可以选用非常便宜的舵机，例如MG996。

* 舵机参数可配置，最大最小PWM值，正反方向等，可以任意安装舵机。

* 3D打印结构，被设计为非常适合使用3D打印机打印。

* 快拆结构，直接徒手拆先天线支架，一颗手拧螺丝拆卸水平旋转结构，方便携带与收纳。

* 1/4螺孔，嵌入1/4英寸螺母，方便安装于三脚架上。

* 水平尺，自带水平泡，用于调整安装时的水平位置。

* 双180°舵机，通过翻转实现360°跟踪。

* OLED屏幕，可以显示当前云台的一些状态信息。

* 5向按键操作，通过5向按键可以非常方便的进行各种操作与设置。

* 手动模式，在手动模式下，通过5向按键，可以很方便的控制AAT的指向，适用于超远距离人肉跟踪。

* BB响，提供一些警告与提示音。

* 全彩LED指示灯，在不同的状态下会有不同的颜色闪烁与提示。

* WIFI互联，接入到wifi热点，实现互联，无需繁琐的接线。

* SmartConfig一键配置WIFI。

* 通过遥测数传数据获取飞行器位置信息，无需机载端模块。

* 后续通过扩展模块也可以支持通过图传信道传输遥测数据。

* 多协议支持，S.Port，Raven Telemetry，LTM（即将支持），MSP（开发中），MavLink（开发中）

* 协议与IO口自由配置（开发中）。

* 本地位置通过手机GPS定位，无需外接本地GPS（后续也会支持外接本地GPS模块）。

* 缓冲效果，可以有效的保护舵机，并且缓解急加速急停带来的抖动，缓冲效果参数可配置。

* 电池电压监控，支持2S电池与3S电池，监控参数可配。

* 基于GPS轨迹数据的位置预估系统（开发中）

* APP支持，目前APP仅有简单的飞行数据显示，其他功能正在开发中。

* 集成RX5808图传接收模块（计划中）

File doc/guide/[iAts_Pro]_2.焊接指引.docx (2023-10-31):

焊接指引

2019-10-27

更新BOM表到v2.2.1版本，修改焊接说明将LM7805替换为SX2106

2020-08-04

更新BOM表到v3.0版本，去掉了容易爆炸的钽电容

所需工具：

1. 焊台（烙铁推荐使用刀头老司机随意）
2. 热风枪
3. 排烟气扇
4. 尖头镊子
5. 剪刀
6. 口罩
7. 放大镜
8. 其他（牙签，纸巾，酒精等）

材料：

1. PCB空板
2. BOM表上所有所需元件（BOM表看这里）
3. 焊锡
4. 锡膏

准备工作：

将工作台清理干净，工具依次有序的放在方便拿取的地方（个人习惯：焊台在正前方偏右，工具在右手边区域），元件分类整理做好标识，并放在方便拿取的地方（个人习惯：元件一般阻容等分类放在左手边区域），由于有铅焊锡含铅，并且铅有毒性，另外焊锡中松香挥发的烟气会刺激呼吸道，所以请做好个人防护工作，保持房间通风，打开排烟气扇并戴上口罩。

推荐焊接步骤：

1. 所有0603的阻容，LED，二极管，三极管，电源稳压芯片RT9013，SX2106
2. CP2102，Micro USB座，WS2812，电感
3. ESP32模组
4. OLED屏幕
5. XT30，FPDK电源模块，5向按键，BB响，排针

焊接过程：

焊接推荐使用锡膏加热风枪，这样焊接出来的板子比较干净，没有松香融化在板子上产生的痕迹，并且速度上也比用烙铁焊接略快一些。

先将当前需要焊接的所有元件的焊盘上使用牙签刮上薄薄的一层锡膏，注意锡膏的厚度，太多了会产生锡珠，太少了有可能焊不稳。刮完锡膏之后，将所对应的元件放到对应的焊盘上，有方向或极性的元件，注意对好丝印上的方向与极性。元件摆放好之后，将热风枪调到350度，并开到最小风力，对PCB进行加热，使锡膏融化，锡膏融化后，元件会受到液体表面张力而自动对准焊盘的位置，同时也可以使用镊子轻微调整，之后等待PCB冷却即可。

QFN封装的CP2102焊接对于新手来说有一定难度，注意锡膏一定要适量，可以将锡膏挂到焊盘的最外围，这样锡膏融化后会沿着焊盘流到芯片引脚下面，锡膏如果过多，会出现引脚间连锡的现象，不用担心，待锡膏冷却后，使用烙铁轻轻的在连锡的引脚间刮一下即可。

ESP32模组与FPDK模块底部有散热的焊盘，可以抹上少量导热硅脂增加导热性能。WS2812不太耐热，建议等锡膏融化之后，再立即将原件放到焊盘上。

每一步完成之后，一定要再次检查极性元件的焊接是否正确，并且需要做对应的测量与测试工作，以保证焊接的正确性，以免产生意外并造成更大的损失。

测量与测试：

第一步完成后

1. 使用万用表通断档分别测量5V丝印位置的焊盘与3.3V测试点对地是否有导通，如果有导通，请检查是否有连锡、元件损坏造成的短路。
2. 通过XT30焊盘给板子进行12V的供电，观察标识R的LED灯是否正常点亮，如果未正常点亮，检查SX2106与RT9013稳压芯片。
3. 使用万用表直流电压档分别测量5V丝印位置与3.3V测试点位置的电压是否正常，如果不正常，检查SX2106与RT9013稳压芯片。

第二步完成后

1. 通过USB线将板子连接到电脑，标识R的LED灯应该会亮起，如果未点亮，检查SS14二极管是否焊反了。
2. 连接到电脑后，打开电脑的设备管理器，如果CP2102焊接正确，切电脑是win7以上的系统，应该会自动安装驱动，并在串口选项卡中出现对应的设备，如下图：
3. 固件下载完成后，断电再上电，WS2812应该会亮白光，并闪烁3下，说明程序已经正常启动。

第三步完成后

1. 使用万用表的通断档，测量每个相邻的焊点，保证没有连锡。
2. 通过USB线将板子连接到电脑，尝试下载固件，板子上设计自动复位电路，所以

不需要进行手动复位即可自动开始下载固件。

第四步完成后

1. 使用万用表的通断档，测量每个相邻的焊点，保证没有连锡，注意：有部分引脚本身是相连的，请参考下图进行测量：
2. 对设备进行上电，如程序正常启动，OLED上出现开机画面，否则请检查焊接是否正确。

第五步完成后

1. 使用万用表电压档测试舵机输出排针V与G之间的电压，如果为5V则正常。
2. 通过XT30接口给板子上电，正常屏幕会出现开机动画，WS2812亮白光后闪烁，BB响会响5下。

各版本BOM表：

元件位图：

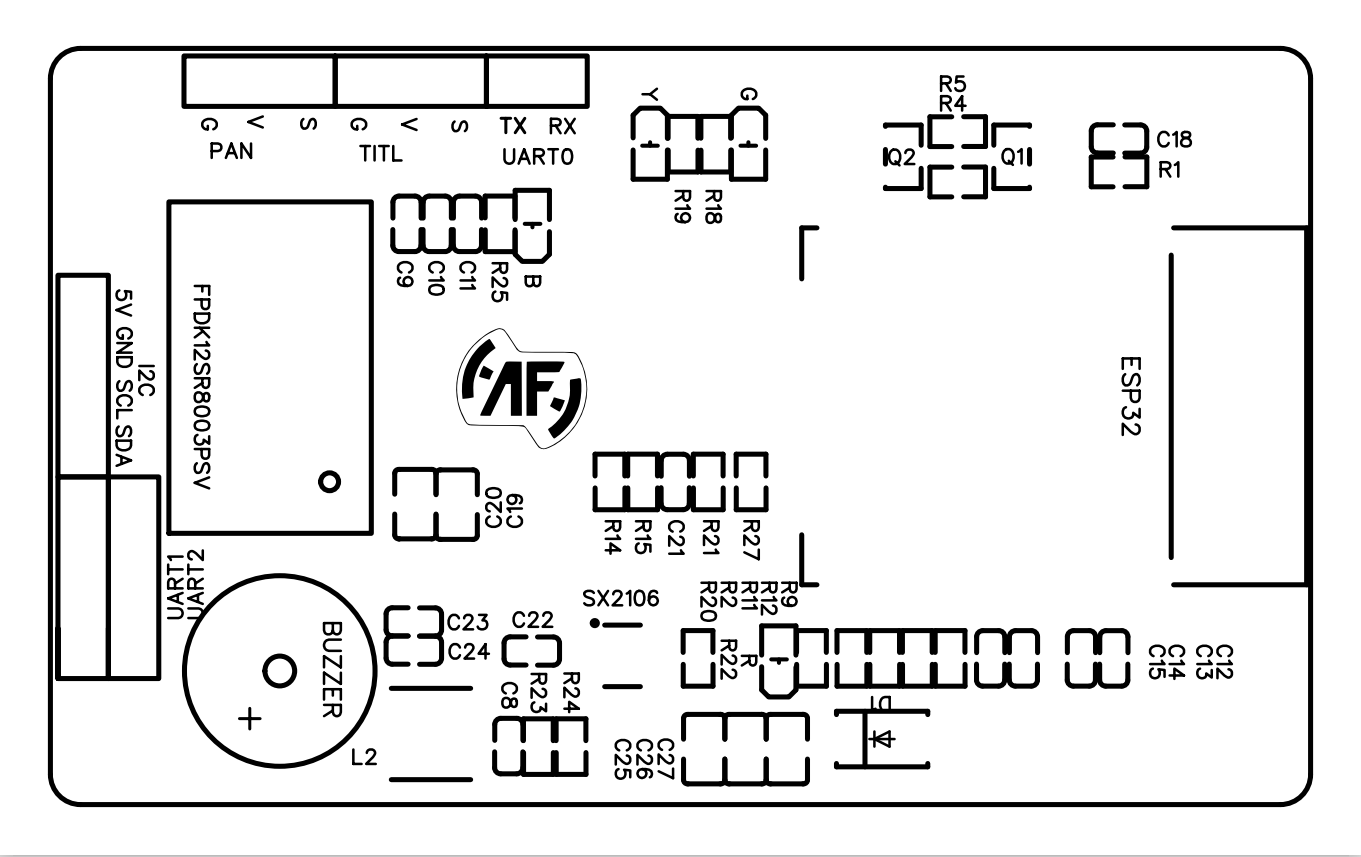
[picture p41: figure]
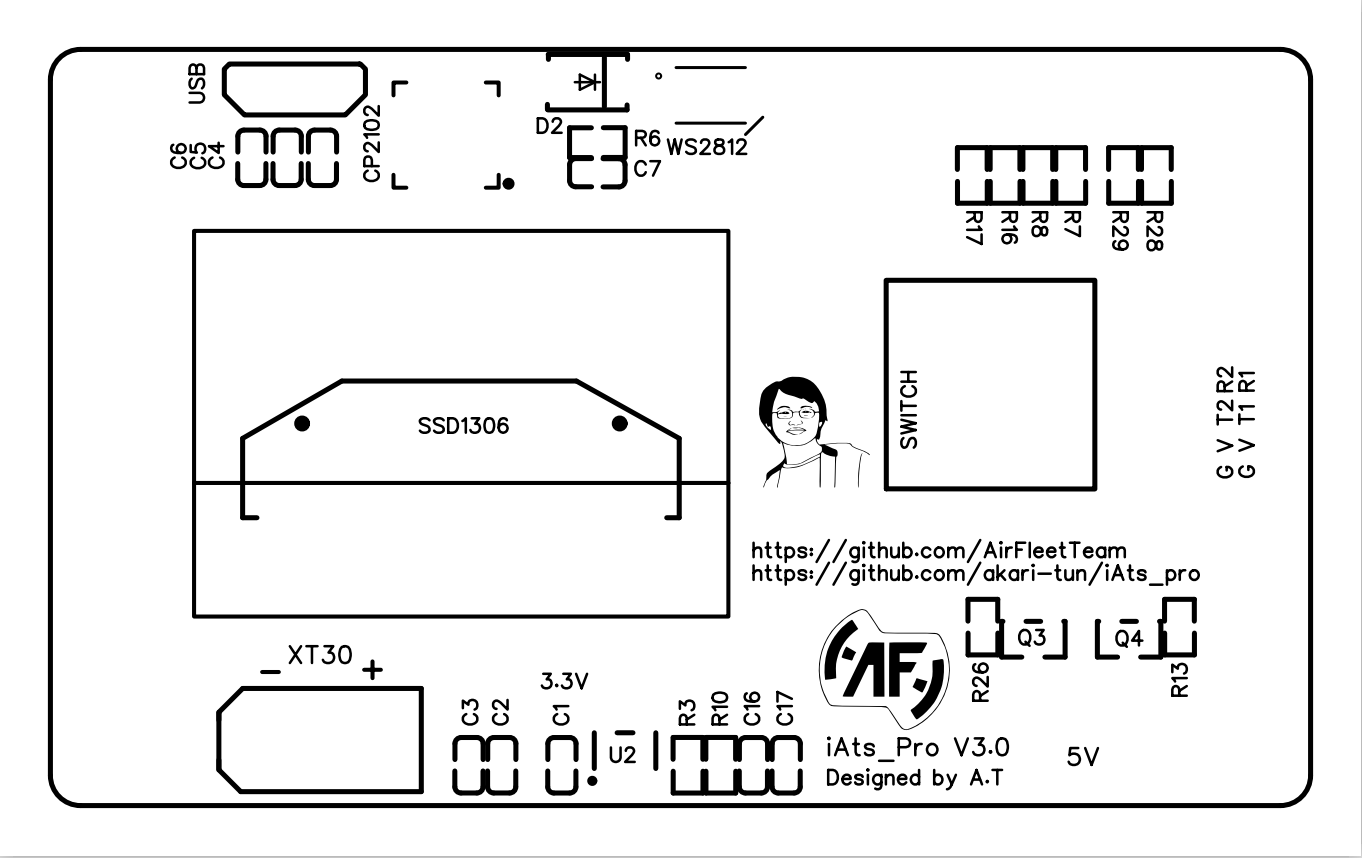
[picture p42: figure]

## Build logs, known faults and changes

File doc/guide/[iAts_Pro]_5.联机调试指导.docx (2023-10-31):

联机调试指导

2020-08-04

更新更简单的调试方式，直接通过串口输入NMEA格式的GPS数据即可方便的进行调试。

此文档主要介绍了如何在PC上使用相关的工具对AAT进行调试，通过相关的模拟工具，可以模拟AAT工作时的情况。所以，在正式使用前，最好先在PC上调试正常。

所需软件：

1. iAts_Server

使用.net framework框架编写的windows平台窗体程序，可以在此项目的Github仓库中下载到：https://github.com/akari-tun/iAts_pro/blob/master/tools/iAts.Server.zip

如果是win10以下的系统，需要安装 .Net Framework 4.6：

https://dotnet.microsoft.com/download/dotnet-framework/net462

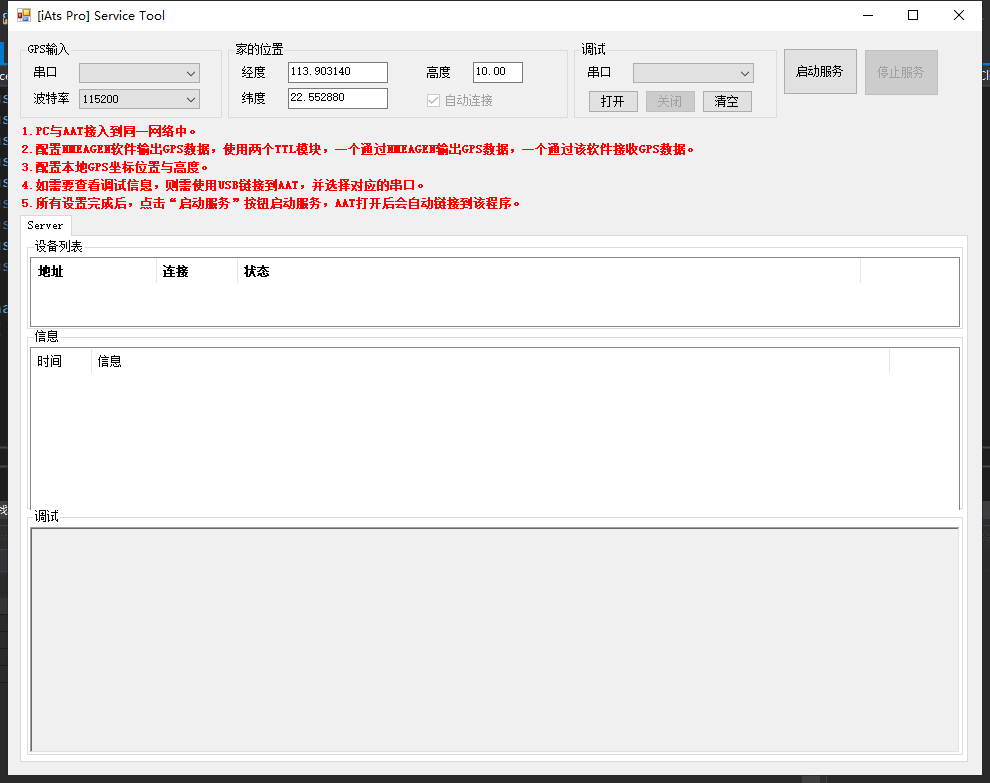
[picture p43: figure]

2. NMEAGEN

GPS数据模拟软件，可以输出NMEA协议的GPS数据，压缩包中已经提供了该程序。

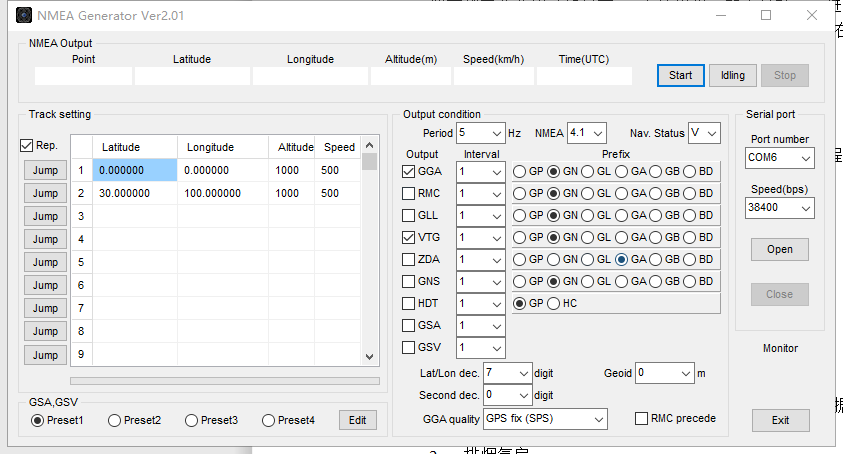
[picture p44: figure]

所需工具：

1. 两个USB转串口TTL模块（推荐CP2102模块）

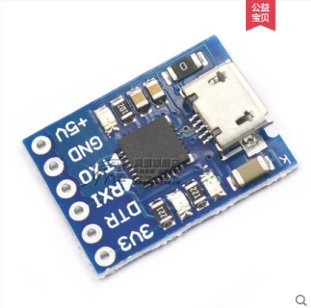
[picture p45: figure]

准备工作：

AAT连接好WIFI（WIFI的连接方法请参考使用说明），并确保所连接的WIFI与PC在同一网络中，最好PC与AAT连接到同一个路由器而不是连接到路由器接出来的AP，有些AP模式不会转发UDP广播报文，会导致AAT与调试工具无法正常连接。

将USB转TTL模块与PC进行连接，安装好驱动，并将两个TTL模块的TX与RX使用杜邦线交叉连接。

RX<-----TX

TX----->RX

因为都连接到同一PC，已经共地了，所以GND就不用接了。

软件设置：

1. NMEAGEN软件设置

打开NMEAGEN软件，左侧是需要模拟的GPS坐标，可以输入N个坐标，最好是输入一个绕圈的坐标，再有一个走过中心点的坐标，这样方便模拟AAT在各个不同方位指向的角度是否正确。

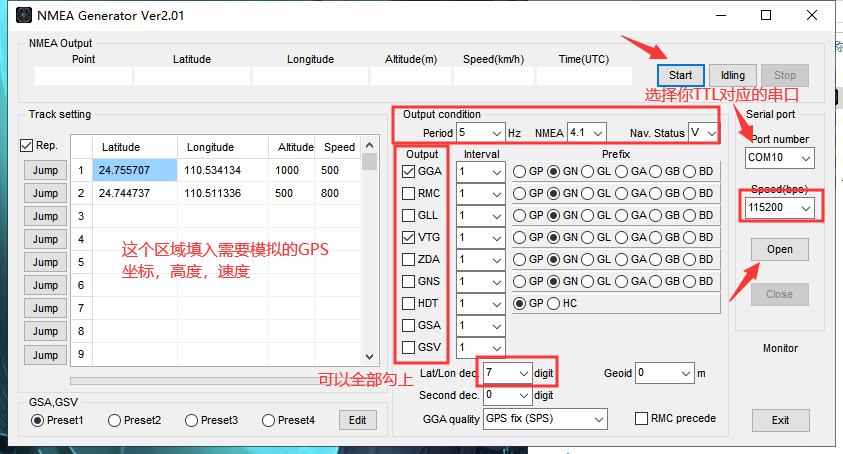
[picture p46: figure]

2. 调试工具设置

GPS输入：这里填入两个TTL中的其中一个（不是NMEAGEN软件中的那个），用于接收NMEAGEN软件输入的GPS数据，注意波特率需要一致。

家的位置：这里输入AAT的坐标位置与高度，工具会将坐标位置发送给AAT，AAT会以此为家的位置来进行跟踪。

调试：用于监控调试数据，使用MicroUsb插入AAT板上的USB接口，注意需要选择正确的串口，AAT中的串口调试信息会通过这个串口进行输出。

设备列表：这个列表框中会显示成功连接上的AAT信息，右键点击会弹出菜单，可以对AAT进行参数设置。

信息：这个区域会显示AAT与调试程序之间的交互数据。

调试：输出AAT的调试信息。

请参考下面的图片进行设置

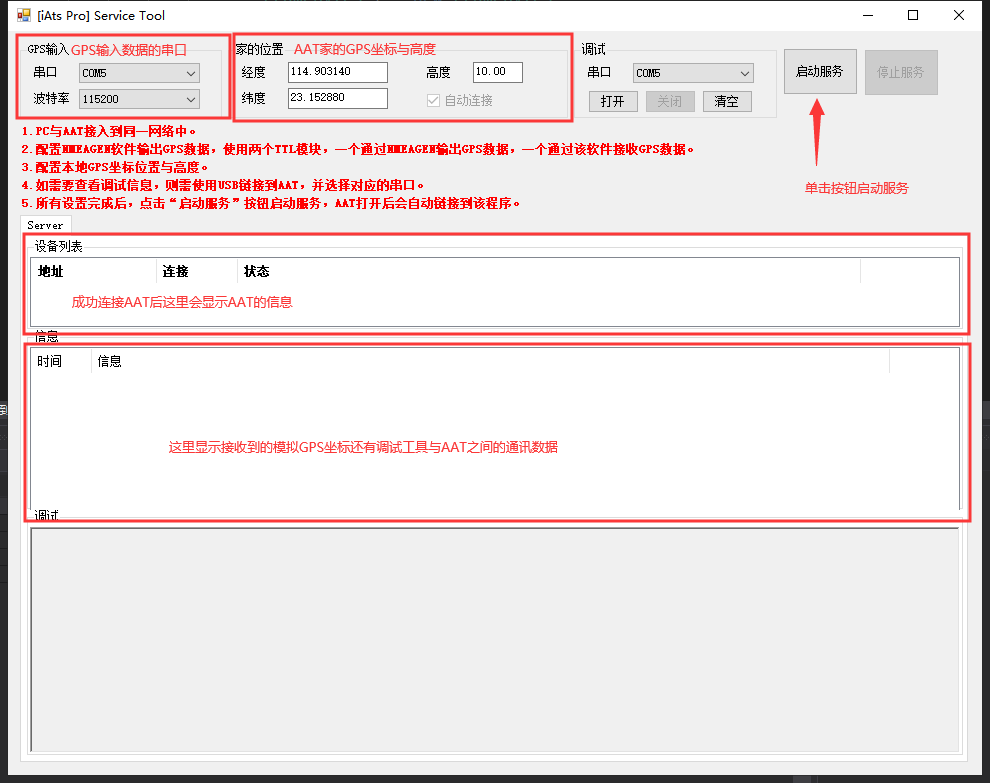
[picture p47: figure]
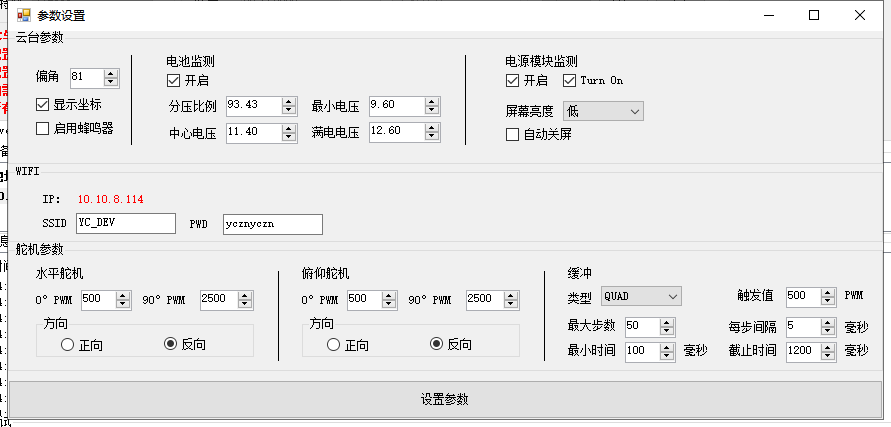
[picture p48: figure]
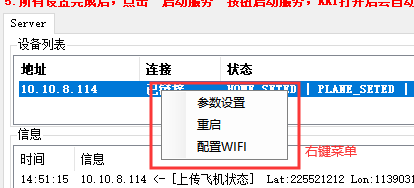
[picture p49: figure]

AAT设置与连接：

AAT上电，联机调试需要AAT连接WIFI，请在设置中打开 WIFI->Enable：On，

成功连接WIFI后，AAT会使用UDP协议向网络中发送心跳广播，心跳中会包含AAT的 连接地址与端口信息，调试工具接收并成功解析到心跳广播后，会向AAT发送相应的 心跳应答信息，如此，AAT与调试工具可实现自动连接。

AAT成功连接后，如果没有设置HOME位置，会向调试工具请求HOME位置，调试工具会将所设置的HOME位置下发给AAT，AAT成功获取到HOME之后，蜂鸣器会短鸣一声，并在主界面左上角显示一个小房子的图标。

AAT参数调整：

在AAT主界面，双击中键进入手动模式，此时使用五向案件可以控制AAT的水平舵机与俯仰舵机，这样方便进行参数的调整。

1. 舵机方向调整

向右拨动五向按键，观察水平转动的方向是否正确，水平角度由小到大，正确的方向应该是顺时针旋转，如果转动方向不正确，需要在Servo->Pan->Direction这个参数调整，Forward是舵机正向，Reverse是舵机反向。

上下拨动五向按键，使俯仰处于0度位置，观察俯仰舵机的方向，屏幕面对自己，在水平方向0度时，俯仰方向需要指向前方，90度时，俯仰方向指向右方，180度时，俯仰方向指向自己，270度时，俯仰方向指向左方，如果反向不正确，在Servo->Pan->Direction这个参数调整正反。

2. 调整缓冲，使翻转更平稳

Servo->Ease 菜单下，有缓冲的调整，几种缓冲类型的效果，可以在这个地址看到：http://www.gizma.com/easing/

通过参数Servo->Ease->Type参数可以选择各个不同的效果，其他参数的说明如下。

Max Steps：缓冲步数，从舵机的运动开始，到结束，总共进行多少步的PWM输出。

Min PWM：使用缓冲效果的最小PWM，目标PWM - 当前PWM >这个值才会执行缓冲效果。

Step MS：每步缓冲的间隔，每输出一个PWM，需要等待舵机运动到位置后，再执行下一步，这个参数就是控制每输出一步之后，等待多长时间再输出下一步，单位是毫秒。

Max MS：缓冲的最长时间，如果Max Steps * Step MS > Max MS，那么缓冲每步的等待时间Step MS = Max MS / Max Steps。

Min MS：缓冲的最短时间，Max Steps * Step MS < Max MS，那么缓冲每步的等待时间Step MS = Min MS / Max Steps。

3. 电压校准

首先使用万用表量出电池的电压作为参考，使用五向按键选择到菜单：

Tracker->Monitor->Battery->V.Scale

左右拨动五向按键修改分压比例值，长按中键确认设置，设置之后观察Voltage显示的值，直到该值与测量出的电池电压一致，电压即校准完成。

主屏幕右上角的电池电量图标百分比是靠以下三个参数控制：

Max V.：电池满电的电压，如果是3S供电就是12.6，电压在这个值或高于这个值，电池显示满电。

Min V.：电池空电电压，电压小于这个值，电池显示空电。

Center V.：电压中位，因为不同的电池放电曲线不相同，所以设置此值，为电压的中位数，高于与低于此中位数的值分别进行计算。

4. 舵机中位调整

双击中键盘切换到手动模式，在手动模式下进行舵机中位的调整。

水平舵机中位调整：

使水平舵机处于0度的位置，观察支架是否与外壳平行，如果不平行，调整参数Servo->Pan->Min PWM，直到支架与外壳平行。

使水平舵机处于179度的位置，观察支架是否与外壳平行，如果不平行，调整参数Servo->Pan->Max PWM，直到支架与外壳平行。

注意，如果参数Direction设置的是Reverse，则0度与179度位置调整的参数需要互换。

俯仰舵机调整：

使俯仰舵机处于0度的位置，观察天线支架是否与舵机支架垂直，如果不垂直，调整参数Servo->Pan->Min PWM，直到垂直。

使俯仰舵机处于90度的位置，观察天线支架是否与舵机支架处于一条直线，如果不，调整参数Servo->Pan->Max PWM，直到处于一条直线。

注意，如果参数Direction设置的是Reverse，则0度与179度位置调整的参数需要互换。

模拟测试：

一切准备就绪，单击NMEAGEN软件的Start按钮启动模拟数据输出，所输出的GPS坐标数据会通过串口发送调试工具，调试工具解析后，会将相关的指令发送给AAT，AAT将会计算对应的角度并控制舵机指向对应的角度。

更方便的调试方式：

现在AAT已经可以支持通过串口直接输入GPS数据进行模拟测试，按照上面NMEAGEN软件设置好之后，将TTL模块的TX与GND分别插入AAT侧面的两个串口其中一个的RX与GND，之后进入设置界面:

Port->UART1（或2）

Enable：修改为On

Type：修改为Input

Protocol：修改为NMEA

Baudrate：修改为与软件设置的一致

如果一切配置正确，那么这时候在AAT的主界面上应该能看到有坐标显示，此时需要先设置家的位置：

Tracker->Home->Set Home->Confirm

确认后，会将当前的坐标记为家的位置，设置完成后，如果坐标数据都正确，那么这时候AAT应该已经开始跟踪。

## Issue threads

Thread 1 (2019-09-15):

KiCad or Gerber files available?

careyer, 2019-09-15:
Hi there,

this looks like awesome project and I am considering putting some of my ESP32 sitting on the shelf to good use. Do you think it is possible to share design files of the PCB (Gerbers or KiCad or anything that allows to order a small number of those boards with a PCB manufacturer)?

Thank you very much in advance!
Best regards!
Thomas

akari-tun, 2019-09-16:
I am glad you are interested in my project. This project is still development on the way,So the PCB is also in continuous improvement.You can give me your e-mail here, and I will send you the Gerber file of the last version.

careyer, 2019-09-16:
Hi TanJun, thank you for coming back to me! Your friend DusKing was kind enough to contact me via Telegram and offered to forward my email address to you so I don't have to publish it in public (you know... bots, spam and all sorts of nasty stuff  ;-). I think he will reach out to you the next days and give you my email. Are you on Telegram as well?

Best regards and keep that great project going.

P.S: I have browsed the repository or your arduino based tracker just yesterday and it is so well documneted! That is really awesome. I was just struggling a bit with the chinese fonts. Happy to see that you do this one in english language.

akari-tun, 2019-09-17:
Hi Thomas, DusKing was gived me your email address at last night, I sended the files of this project to you just now. I written few documents for this project in Chinese language, and so sorry for I don't have enough time to write documents in English recently. If you need anything other,please tell me.

Before you provide the Gerber files to the manufacturer, you must check the Bom of V2.2 and make sure all components can easy to buy. I used an old second-hand power module "FPDK12SR8003PSVP".
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
I bought this module easily and cheaply on www.taobao.com, I don't know if you can easily to buy this module. I plan to replace this module with "MP9443", which is a good power IC, but it a little expensive.

careyer, 2019-09-17:
Oh wow! Thanks! ... Your word of warning is much appreciated. Indeed the FPDK12SR8003PSVP can not be purchased anywhere here. From what I can tell it is long EOL. I could not find the "MP9443" either though (just a Yamaha Termosensor that is called exactly like this ;-).
Maybe consider a readily avialable part here. I think what you need is a DC-DC converter right?
So I better wait for the final version then so that we stay compatible and can share test results.
Many thanks in advance and keep that awesome project going!

akari-tun, 2019-09-17:
Oh sorry, I wrote a wrong word! It's "MP9447" , A DC-DC converter IC. It can provide 5A current, I think can adapter most of the sevro requirements .
I will modify it as soon as possible and other components can you easily to buy?

careyer, 2019-09-17:
Alright! Now MP9447 looks much better suited for the job ;-). I can source this here no problem. However It looks like a BGA package design, is it?  I think for the ease of use and to enable more people to rercreate this design it would be better to choose "ordinary" ICs with legs - they just solder so much easier.
Other than that I skimmed through the BOM and found the CP2102-GMR to be also BGA design, is it? The RT9013-33GB seems to be availible only in China as well. There is no way in getting it from a distributor nearby.
All other parts should not give any problems and are readily availible.

Best regards! Have a good day.
Thomas

akari-tun, 2019-09-18:
I think MP9447 and CP2102 belong to QFN package, but it is impossible to solder with soldering iron.
I recommend soldering with solder paste, appropriate amount of solder paste and melting it with a heat gun.

The CP2102 is not required,I brought out UART0 with 2.54mm pin and download program through an external USB to TTL module, but it's not too convenient to use, so I Integrated it in board.

If the RT9013-33GB can't buy easily then I need to choose a new 3.3v LDO IC.I think most of MPS's products can easily to buy from all of the world？

Thanks for your wishes and you have a good day too.

Closed 2023-10-08.

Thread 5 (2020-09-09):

STL files available

Seeelefant, 2020-09-09:
Dear akari-tun,
can you make the stl files available?

akari-tun, 2020-09-09:
Hi,thanks for interest in my project.
I will push the stl files to this repositorie recently.

Seeelefant, 2020-09-09:
Thank you TanJun, these will be helpful for  all who are interested in your project 👍

akari-tun, 2020-09-11:
> Thank you TanJun, these will be helpful for all who are interested in your project 👍

I have uploaded the STL file and provided the STP file that can be modified.

Seeelefant, 2020-09-13:
Hi Tan-Jun, I started to print right away and things look very good. Do you think it is possible to share design files of the PCB (Gerbers or KiCad or anything that allows to order a small number of those boards with a PCB manufacturer)?
Best
Seeelefant

akari-tun, 2020-09-18:
Ok, I have uploaded BOM and Gerber files.

akari-tun, 2020-09-18:
I have written some documents in Chinese, and I plan to translate them into English soon and commit them to this repository.

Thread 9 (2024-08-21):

屏幕一直检测不到

Scarittagle, 2024-08-21:
作者你好，我们尝试按照您的硬件搭建了一个我们自己的硬件 大体上基本都是一样的 除了SSD1306屏幕的地址变成了0x78.
但是在代码里把ADDR更改成了0x78之后却依旧显示no screen detected, 而且也有发现好像screen i2c用的是16，17针脚而非原理图上的32，33针脚，所以哪个才能用的呢

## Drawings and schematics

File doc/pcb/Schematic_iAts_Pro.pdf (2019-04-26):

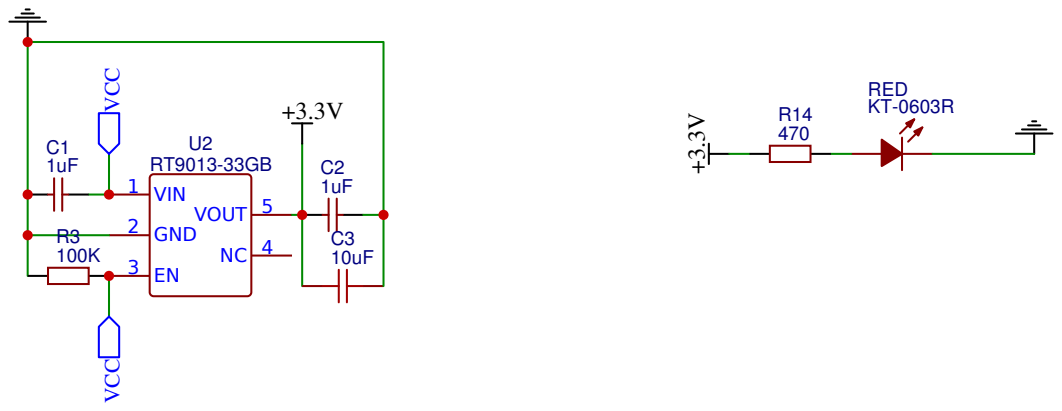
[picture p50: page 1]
TITLE:; REV: 1.0; Date:; Sheet: 5/5 Drawn By: akari_tun; Company: AirFleet; VIN 1; GND 2; VOUT 5; VCC VCC; RED

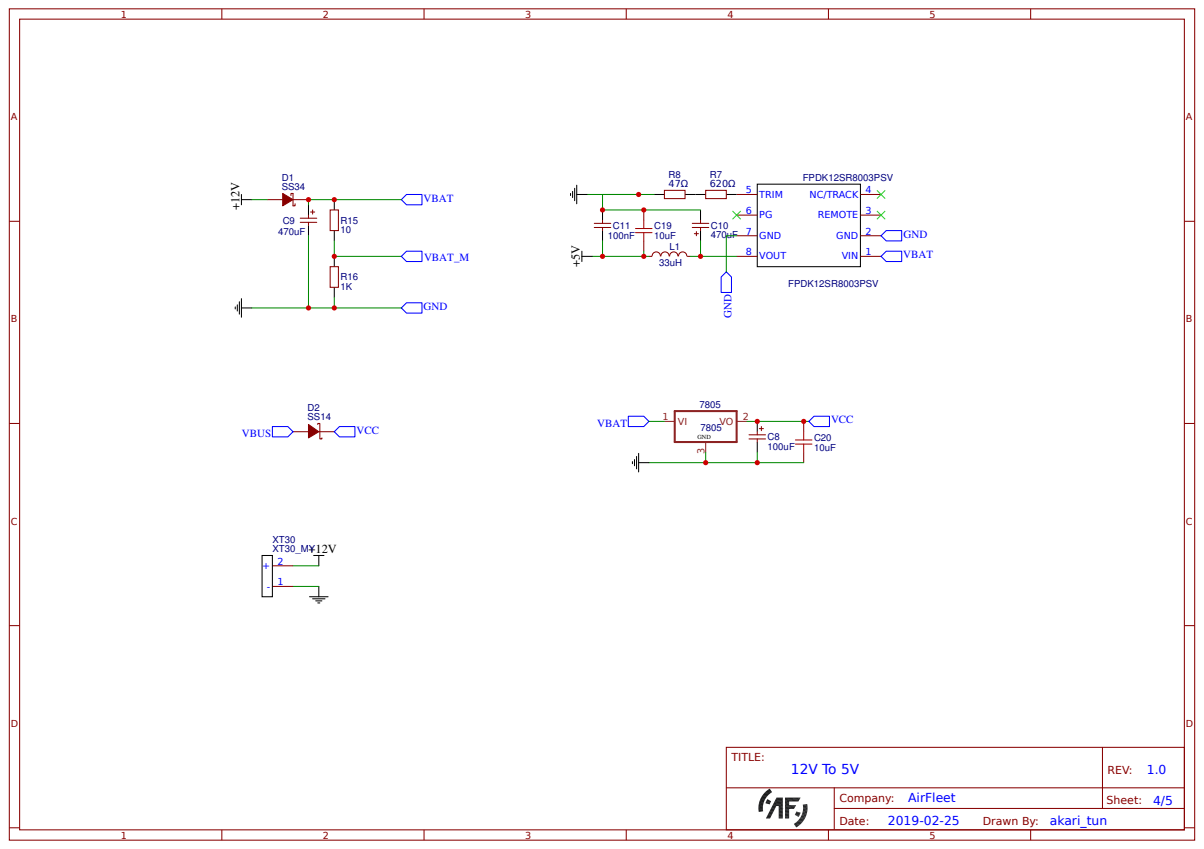
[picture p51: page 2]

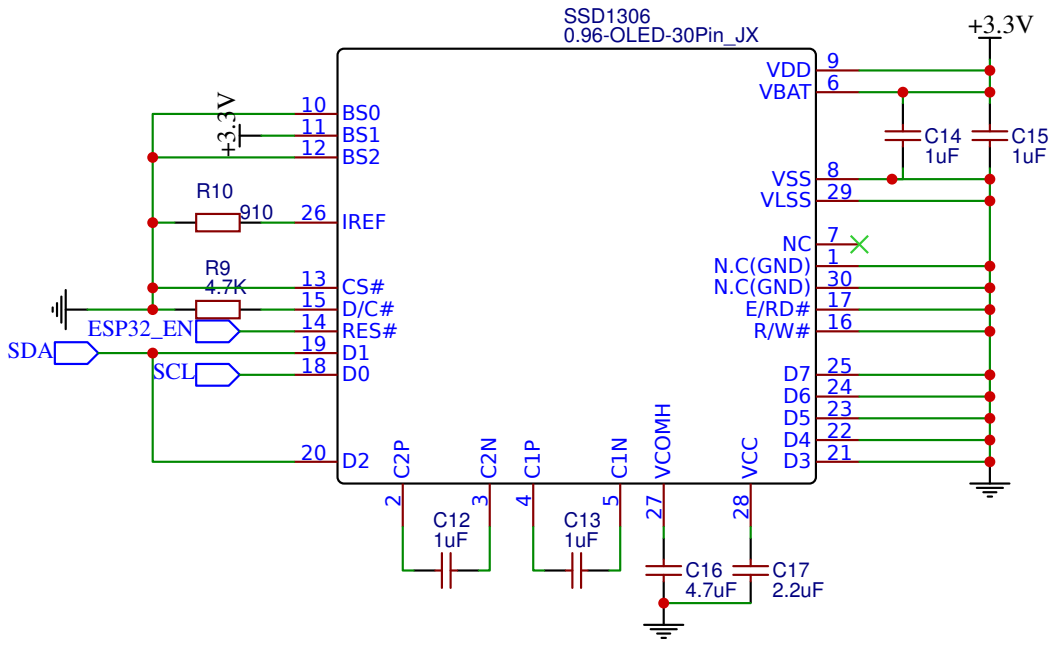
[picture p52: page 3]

R/W# 16 E/RD# 17 N.C(GND) 30 N.C(GND) 1 NC 7

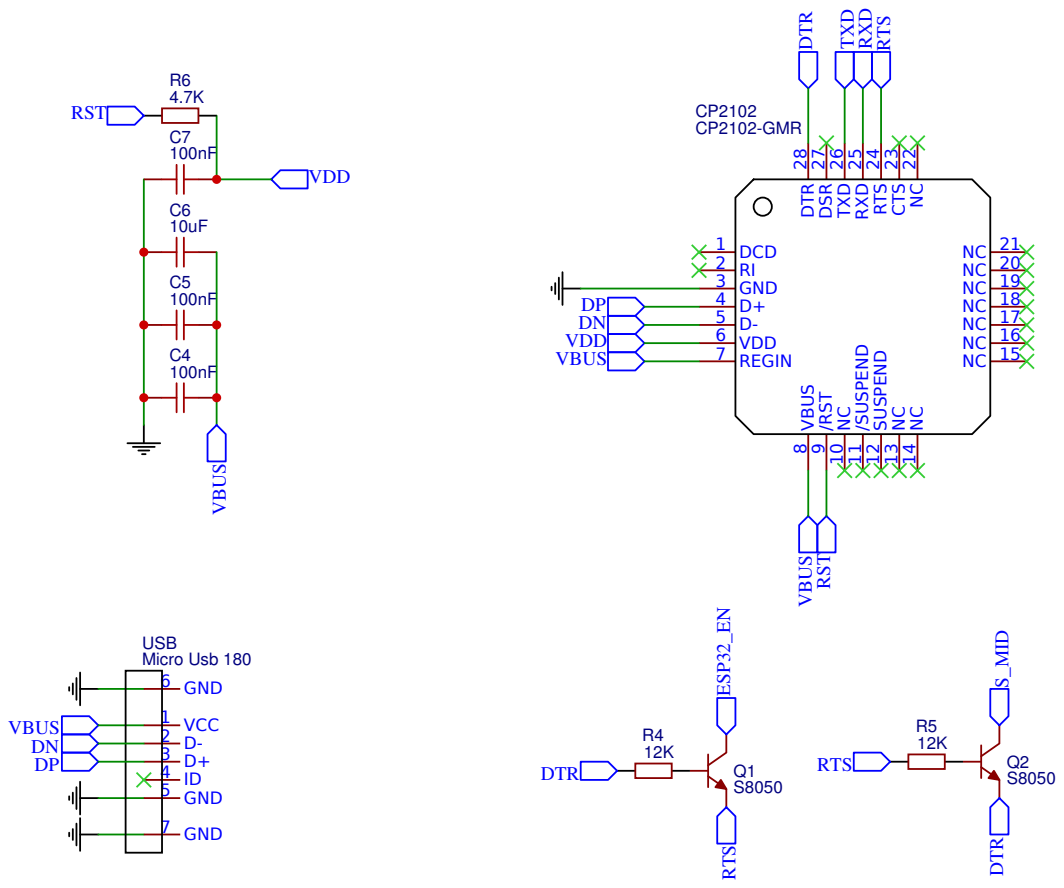
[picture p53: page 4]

NC 22 CTS 23 RTS 24 RXD 25 TXD 26 DSR 27 DTR 28 DTR TXD RXD RTS

IO0 25 IO4 26 IO16 27 IO17 28 IO5 29 IO18 30 IO19 31 NC 32 IO21 33 RXD0 34 TXD0 35 IO22 36 IO23 37 GND 38

+3.3V

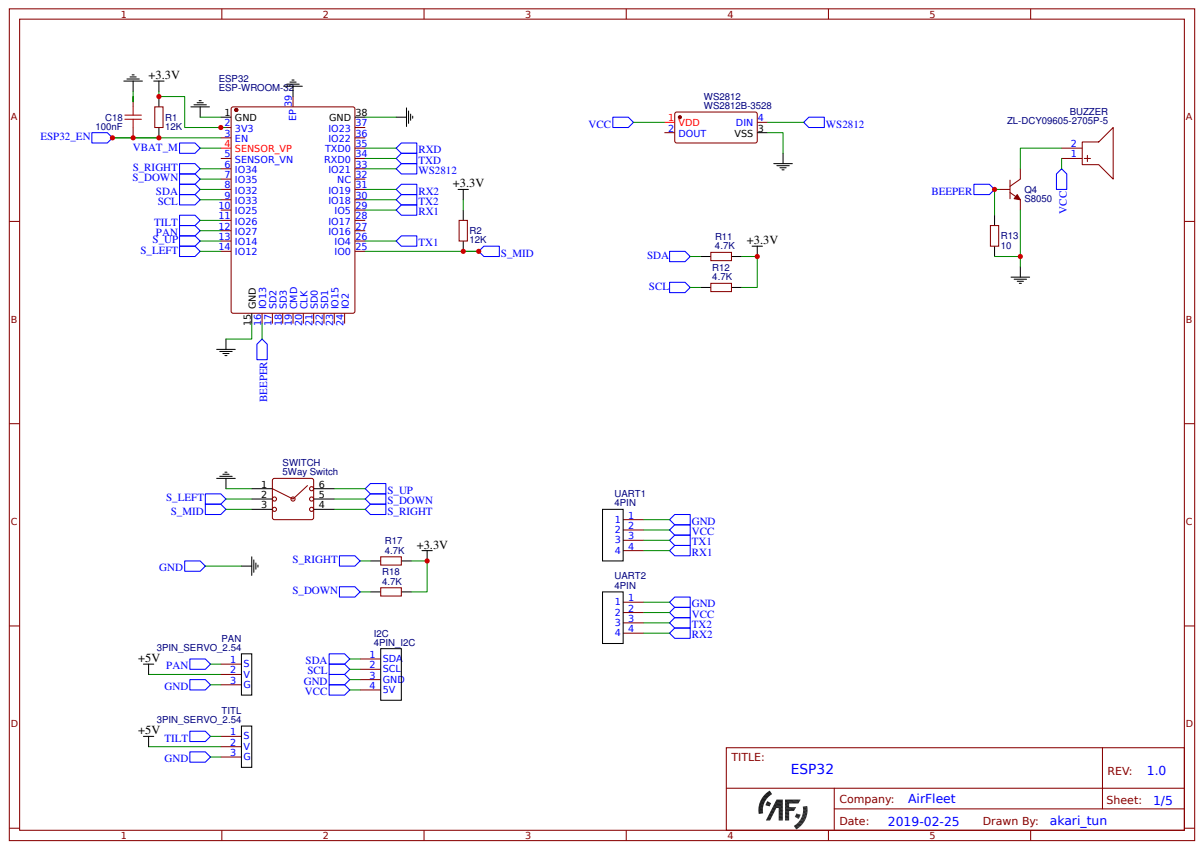
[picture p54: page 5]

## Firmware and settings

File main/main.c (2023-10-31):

#include <stdio.h>

#include <hal/log.h>
// #include "esp_task_wdt.h"
#include "freertos/FreeRTOS.h"
#include "freertos/task.h"
#include "esp_attr.h"

#include "platform/system.h"

#include "driver/mcpwm.h"
#include "soc/mcpwm_reg.h"
#include "soc/mcpwm_struct.h"

#include "target/target.h"

#include "ui/ui.h"
#include "ui/led.h"
#include "ui/beeper.h"
#include "wifi/wifi.h"
#include "config/settings.h"
#include "tracker/tracker.h"
#include "tracker/servo.h"
#include "protocols/atp.h"

#include "util/time.h"
#include "util/macros.h"

#include "io/hal_i2c.h"

#include "sensors/imu_task.h"

static ui_t ui;
#if defined(USE_WIFI)
static wifi_t wifi;
#endif
static tracker_t tracker;
static hal_i2c_config_t i2c_0_cfg;
static hal_i2c_config_t i2c_1_cfg;

static void setting_changed(const setting_t *setting, void *user_data)
{
    UNUSED(user_data);

    if (SETTING_IS(setting, SETTING_KEY_DEVELOPER_REBOOT))
    {
        system_reboot();
    }
}

void iats_tracker_init(void)
{
	tracker_init(&tracker);
}

void iats_ui_init(void)
{
	ui_config_t cfg = {
		.buttons = {
			[BUTTON_ID_ENTER] = BUTTON_CONFIG_FROM_GPIO(BUTTON_ENTER_GPIO),
#if defined(USE_BUTTON_5WAY)
			[BUTTON_ID_LEFT] = BUTTON_CONFIG_FROM_GPIO(BUTTON_LEFT_GPIO),
			[BUTTON_ID_RIGHT] = BUTTON_CONFIG_FROM_GPIO(BUTTON_RIGHT_GPIO),
			[BUTTON_ID_UP] = BUTTON_CONFIG_FROM_GPIO(BUTTON_UP_GPIO),
			[BUTTON_ID_DOWN] = BUTTON_CONFIG_FROM_GPIO(BUTTON_DOWN_GPIO),
#endif
		},
#if defined(USE_BEEPER)
		.beeper = BEEPER_GPIO,
#endif
#ifdef USE_SCREEN
		// .screen.i2c_bus = SCREEN_I2C_BUS,
		// .screen.sda = SCREEN_GPIO_SDA,
		// .screen.scl = SCREEN_GPIO_SCL,
		//.screen.i2c_cfg = tracker.imu->available ? &i2c_1_cfg : &i2c_0_cfg,
		.screen.i2c_cfg = &i2c_1_cfg,
		.screen.rst = SCREEN_GPIO_RST,
		.screen.addr = SCREEN_I2C_ADDR,
#endif
	};

#ifdef USE_SCREEN
	if (!ui_screen_init(&ui, &cfg, &tracker))
	{
		ui.internal.screen.internal.is_init = false;
		if (!tracker.imu->available) i2c_0_cfg.freq_hz = SCREEN_I2C_MASTER_FREQ_HZ;			
		cfg.screen.i2c_cfg = &i2c_0_cfg;
		ui_screen_init(&ui, &cfg, &tracker);
	}
#endif

#if defined(USE_WIFI)
	ui_init(&ui, &cfg, &tracker, &wifi);
#else
	ui_init(&ui, &cfg, &tracker);
#endif
	led_mode_add(LED_MODE_BOOT);
}

#if defined(USE_WIFI)
void iats_wifi_init(void)
{
	wifi_init(&wifi);
	wifi.t = tracker.atp;
	wifi.callback = tracker.atp->atp_decode;
	tracker.atp->atp_send = wifi.send;
}
#endif

void iats_i2c_init(void)
{
	i2c_0_cfg.i2c_bus = I2C_BUS;
	i2c_0_cfg.scl = I2C_GPIO_SCL;
	i2c_0_cfg.sda = I2C_GPIO_SDA;
	i2c_0_cfg.freq_hz = I2C_MASTER_FREQ_HZ;

	hal_i2c_init(&i2c_0_cfg);

	i2c_1_cfg.i2c_bus = SCREEN_I2C_BUS;
	i2c_1_cfg.scl = SCREEN_GPIO_SCL;
	i2c_1_cfg.sda = SCREEN_GPIO_SDA;
	i2c_1_cfg.freq_hz = SCREEN_I2C_MASTER_FREQ_HZ;

	hal_i2c_init(&i2c_1_cfg);
}

void task_ui(void *arg)
{
	UNUSED(arg);

	if (ui_screen_is_available(&ui))
	{
		ui_screen_splash(&ui);
	}
	
	for (;;)
	{
		ui_update(&ui);
		ui_yield(&ui);
	}
}

void task_io(void *arg)
{
	if (settings_get_key_bool(SETTING_KEY_PORT_UART1_ENABLE) || settings_get_key_bool(SETTING_KEY_PORT_UART2_ENABLE))
	{
		tracker.uart1.io_runing = settings_get_key_bool(SETTING_KEY_PORT_UART1_ENABLE);
		tracker.uart2.io_runing = settings_get_key_bool(SETTING_KEY_PORT_UART2_ENABLE);

		while (tracker.uart1.io_runing || tracker.uart2.io_runing)
		{
			if (tracker.uart1.io_runing)
			{
				tracker_uart_update(&tracker, &tracker.uart1);
			}

			if (tracker.uart2.io_runing)
			{
				tracker_uart_update(&tracker, &tracker.uart2);
			}
		}
	}

	vTaskDelete(NULL);
}

void app_main()
{
	esp_log_level_set("*", ESP_LOG_INFO);

	settings_init();
	settings_add_listener(setting_changed, NULL);

	iats_i2c_init();
	imu_task_init(&i2c_0_cfg);
	tracker.imu = imu_task_get();
	iats_tracker_init();
#if defined(USE_WIFI)
	iats_wifi_init();
#endif
	iats_ui_init();

	xTaskCreatePinnedToCore(tracker_task, "TRACKER", 4096, &tracker, 1, NULL, 1);
	xTaskCreatePinnedToCore(task_ui, "UI", 4096, NULL, 1, NULL, 0);
	xTaskCreatePinnedToCore(task_io, "TRACKER.IO", 4096, &tracker, 1, NULL, 1);
}

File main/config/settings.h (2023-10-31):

#pragma once

#include <stdbool.h>
#include <stdint.h>

#include "config/config.h"
#include "io/gpio.h"
#include "target/target.h"

#define SETTING_STRING_MAX_LENGTH 32
#define SETTING_STRING_BUFFER_SIZE (SETTING_STRING_MAX_LENGTH + 1)
#define SETTING_NAME_BUFFER_SIZE SETTING_STRING_BUFFER_SIZE
#define SETTING_STATIC_COUNT 1
#define SETTING_TEMP_COUNT 15

#define SETTING_TRACKER_FOLDER_COUNT 6
#define SETTING_ESTIMATE_FOLDER_COUNT 2
#define SETTING_ADVANCED_POS_FOLDER_COUNT 2
#define SETTING_HOME_FOLDER_COUNT 9
#if defined(USE_WIFI)
#define SETTING_WIFI_FOLDER_COUNT 6
#else
#define SETTING_WIFI_FOLDER_COUNT 0
#endif
#define SETTING_SERVO_FOLDER_COUNT 2
#define SETTING_SERVO_PAN_FOLDER_COUNT 6
#define SETTING_SERVO_TILT_FOLDER_COUNT 6
#define SETTING_EASE_FOLDER_COUNT 7

#define SETTING_PORT_FOLDER_COUNT 3
#define SETTING_PORT_UART1_FOLDER_COUNT 4
#define SETTING_PORT_UART2_FOLDER_COUNT 4
// #define SETTING_PORT_UART1_FOLDER_COUNT 6
// #define SETTING_PORT_UART2_FOLDER_COUNT 6

#if defined(USE_MONITORING)
#define SETTING_MONITOR_FOLDER_COUNT 1
#else
#define SETTING_MONITOR_FOLDER_COUNT 0
#endif

#if defined(USE_BATTERY_MONITORING)
#define SETTING_BATTERY_FOLDER_COUNT 7
#else
#define SETTING_BATTERY_FOLDER_COUNT 0
#endif

#if defined(USE_POWER_MONITORING)
#define SETTING_POWER_FOLDER_COUNT 4
#else
#define SETTING_POWER_FOLDER_COUNT 0
#endif

#if defined(USE_SCREEN)
#define SETTING_SCREEN_FOLDER_COUNT 3
#else
#define SETTING_SCREEN_FOLDER_COUNT 0
#endif

#if defined(USE_BEEPER)
#define SETTING_BEEPER_FOLDER_COUNT 2
#else
#define SETTING_BEEPER_FOLDER_COUNT 0
#endif

#if defined(USE_IMU)
#define SETTING_IMU_FOLDER_COUNT 4
#define SETTING_IMU_CALIBRATION_FOLDER_COUNT 3
#else
#define SETTING_IMU_FOLDER_COUNT 0
#define SETTING_IMU_CALIBRATION_FOLDER_COUNT 0
#endif

#define SETTING_DIAGNOSTICS_FOLDER_COUNT 2
#define SETTING_DEVELOPER_FOLDER_COUNT 2

#define SETTING_COUNT (SETTING_STATIC_COUNT + SETTING_TRACKER_FOLDER_COUNT + SETTING_ESTIMATE_FOLDER_COUNT + SETTING_ADVANCED_POS_FOLDER_COUNT + SETTING_HOME_FOLDER_COUNT + SETTING_MONITOR_FOLDER_COUNT + SETTING_BATTERY_FOLDER_COUNT + SETTING_POWER_FOLDER_COUNT + SETTING_WIFI_FOLDER_COUNT + SETTING_PORT_FOLDER_COUNT + SETTING_PORT_UART1_FOLDER_COUNT + SETTING_PORT_UART2_FOLDER_COUNT + SETTING_SERVO_FOLDER_COUNT + SETTING_SERVO_PAN_FOLDER_COUNT + SETTING_SERVO_TILT_FOLDER_COUNT + SETTING_EASE_FOLDER_COUNT + SETTING_SCREEN_FOLDER_COUNT + SETTING_BEEPER_FOLDER_COUNT + SETTING_IMU_FOLDER_COUNT + SETTING_IMU_CALIBRATION_FOLDER_COUNT + SETTING_DIAGNOSTICS_FOLDER_COUNT + SETTING_DEVELOPER_FOLDER_COUNT)

#define SETTING_KEY_TRACKER "t"
#define SETTING_KEY_TRACKER_PREFIX SETTING_KEY_TRACKER "."
#define SETTING_KEY_TRACKER_SHOW_COORDINATE SETTING_KEY_TRACKER_PREFIX "show c"
#define SETTING_KEY_TRACKER_REAL_ALT SETTING_KEY_TRACKER_PREFIX "real alt"

#define SETTING_KEY_TRACKER_ESTIMATE SETTING_KEY_TRACKER_PREFIX "e"
#define SETTING_KEY_TRACKER_ESTIMATE_PREFIX SETTING_KEY_TRACKER_ESTIMATE "."
#define SETTING_KEY_TRACKER_ESTIMATE_ENABLE SETTING_KEY_TRACKER_ESTIMATE_PREFIX "Enable"
#define SETTING_KEY_TRACKER_ESTIMATE_SECOND SETTING_KEY_TRACKER_ESTIMATE_PREFIX "E.Sec"

#define SETTING_KEY_TRACKER_ADVANCED_POS SETTING_KEY_TRACKER_PREFIX "e"
#define SETTING_KEY_TRACKER_ADVANCED_POS_PREFIX SETTING_KEY_TRACKER_ADVANCED_POS "."
#define SETTING_KEY_TRACKER_ADVANCED_POS_ENABLE SETTING_KEY_TRACKER_ADVANCED_POS "Enable"
#define SETTING_KEY_TRACKER_ADVANCED_POS_SECOND SETTING_KEY_TRACKER_ADVANCED_POS "A.Sec"

#if defined(USE_MONITORING)
#define SETTING_KEY_TRACKER_MONITOR SETTING_KEY_TRACKER_PREFIX "m"
#define SETTING_KEY_TRACKER_MONITOR_PREFIX SETTING_KEY_TRACKER_MONITOR "."

#if defined(USE_BATTERY_MONITORING)
#define SETTING_KEY_TRACKER_MONITOR_BATTERY SETTING_KEY_TRACKER_MONITOR_PREFIX "b"
#define SETTING_KEY_TRACKER_MONITOR_BATTERY_PREFIX SETTING_KEY_TRACKER_MONITOR_BATTERY "."
#define SETTING_KEY_TRACKER_MONITOR_BATTERY_ENABLE SETTING_KEY_TRACKER_MONITOR_BATTERY_PREFIX "Enable"
#define SETTING_KEY_TRACKER_MONITOR_BATTERY_VOLTAGE SETTING_KEY_TRACKER_MONITOR_BATTERY_PREFIX "Voltage"
#define SETTING_KEY_TRACKER_MONITOR_BATTERY_VOLTAGE_SCALE SETTING_KEY_TRACKER_MONITOR_BATTERY_PREFIX "V. Scale"
#define SETTING_KEY_TRACKER_MONITOR_BATTERY_MAX_VOLTAGE SETTING_KEY_TRACKER_MONITOR_BATTERY_PREFIX "Max V."
#define SETTING_KEY_TRACKER_MONITOR_BATTERY_MIN_VOLTAGE SETTING_KEY_TRACKER_MONITOR_BATTERY_PREFIX "Min V."
#define SETTING_KEY_TRACKER_MONITOR_BATTERY_CENTER_VOLTAGE SETTING_KEY_TRACKER_MONITOR_BATTERY_PREFIX "Center V."
#endif
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

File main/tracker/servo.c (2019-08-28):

#include <hal/log.h>
#include "servo.h"
#include "observer.h"
#include "config/settings.h"

// static const char *TAG = "servo";

void servo_init(servo_t *servo)
{
    servo_pwm_initialize(servo);

    servo->internal.pan.pTr_pulsewidth_cal = &servo_pan_per_degree_cal;
    servo->internal.tilt.pTr_pulsewidth_cal = &servo_tilt_per_degree_cal;
    servo->internal.reverse_notifier = (notifier_t *)Notifier_Create(sizeof(notifier_t));

    uint16_t course = settings_get_key_u16(SETTING_KEY_SERVO_COURSE);
    uint8_t pan_direction = settings_get_key_u8(SETTING_KEY_SERVO_PAN_DIRECTION);
    uint16_t pan_max_plusewidth = settings_get_key_u16(SETTING_KEY_SERVO_PAN_MAX_PLUSEWIDTH);
    uint16_t pan_min_plusewidth = settings_get_key_u16(SETTING_KEY_SERVO_PAN_MIN_PLUSEWIDTH);
    uint16_t pan_max_degree = settings_get_key_u16(SETTING_KEY_SERVO_PAN_MAX_DEGREE);
    uint16_t pan_min_degree = settings_get_key_u16(SETTING_KEY_SERVO_PAN_MIN_DEGREE);
    uint8_t tilt_direction = settings_get_key_u8(SETTING_KEY_SERVO_TILT_DIRECTION);
    uint16_t tilt_max_plusewidth = settings_get_key_u16(SETTING_KEY_SERVO_TILT_MAX_PLUSEWIDTH);
    uint16_t tilt_min_plusewidth = settings_get_key_u16(SETTING_KEY_SERVO_TILT_MIN_PLUSEWIDTH);
    uint16_t tilt_max_degree = settings_get_key_u16(SETTING_KEY_SERVO_TILT_MAX_DEGREE);
    uint16_t tilt_min_degree = settings_get_key_u16(SETTING_KEY_SERVO_TILT_MIN_DEGREE);

    servo->internal.course = course;
    servo->internal.pan.config.direction = pan_direction;
    servo->internal.pan.config.max_pulsewidth = pan_max_plusewidth;
    servo->internal.pan.config.min_pulsewidth = pan_min_plusewidth;
    servo->internal.pan.config.max_degree = pan_max_degree;
    servo->internal.pan.config.min_degree = pan_min_degree;
    servo->internal.tilt.config.direction = tilt_direction;
    servo->internal.tilt.config.max_pulsewidth = tilt_max_plusewidth;
    servo->internal.tilt.config.min_pulsewidth = tilt_min_plusewidth;
    servo->internal.tilt.config.max_degree = tilt_max_degree;
    servo->internal.tilt.config.min_degree = tilt_min_degree;
}

void servo_update(servo_t *servo)
{
    // pan
    servo_pulsewidth_control(&servo->internal.pan, &servo->internal.ease_config);
    // tilt
    servo->internal.tilt.is_reverse = servo->internal.pan.is_reverse;
    servo_pulsewidth_control(&servo->internal.tilt, &servo->internal.ease_config);

    servo_reverse_check(servo);
}

void servo_pulsewidth_out(servo_status_t *status, uint16_t pulsewidth)
{
    if (status->last_pulsewidth != pulsewidth) {
        servo_pwm_out(status, pulsewidth);
    }
    status->last_pulsewidth = pulsewidth;
}

void servo_reverse_check(servo_t *servo)
{
    bool reverse = servo->internal.pan.currtent_degree >= 180;
    if (servo->is_reversing != reverse)
    {
        servo->internal.tilt.is_reverse = reverse;
        servo->internal.pan.is_reverse = reverse;
        servo->is_reversing = reverse;
        servo->internal.reverse_notifier->mSubject.Notify(servo->internal.reverse_notifier, &reverse);
        servo_pulsewidth_control(&servo->internal.tilt, &servo->internal.ease_config);
    }
}

void servo_pulsewidth_control(servo_status_t *status, ease_config_t *ease_config)
{
    uint16_t out_pulsewidth = 0;

    if (!status->is_easing || status->step_positon >= status->step_to) {
        status->currtent_pulsewidth = status->pTr_pulsewidth_cal(&status->config, status->currtent_degree, status->is_reverse);
        uint32_t pwm_error = abs(status->last_pulsewidth - status->currtent_pulsewidth);
        if (pwm_error > ease_config->min_pulsewidth) {
            status->is_easing = true;
            status->ease_start_pulsewidth = pwm_error;
            status->step_positon = 0;
            status->step_to = pwm_error > ease_config->max_steps ?  ease_config->max_steps : pwm_error;
            status->step_sleep_ms = ease_config->step_ms;
            if (status->step_sleep_ms * status->step_to > ease_config->max_ms) status->step_sleep_ms = ease_config->max_ms / status->step_to;
            if (status->step_sleep_ms * status->step_to < ease_config->min_ms) status->step_sleep_ms = ease_config->min_ms / status->step_to;
            out_pulsewidth = servo_ease_cal(ease_config, status);
        } else {
            out_pulsewidth = status->currtent_pulsewidth;
        }
    } else {
        out_pulsewidth = servo_ease_cal(ease_config, status);
    }

    servo_pulsewidth_out(status, out_pulsewidth);
}

uint16_t servo_pan_per_degree_cal(servo_config_t *config, uint16_t degree_of_rotation, bool is_reverse)
{
    degree_of_rotation = degree_of_rotation % config->max_degree;

    uint16_t pwm_of_degree = ((config->max_pulsewidth - config->min_pulsewidth) * degree_of_rotation) / config->max_degree;
    return config->direction > 0 ? (config->max_pulsewidth - pwm_of_degree) : (config->min_pulsewidth + pwm_of_degree);
}

uint16_t servo_tilt_per_degree_cal(servo_config_t *config, uint16_t degree_of_rotation, bool is_reverse)
{
    uint16_t cal_pulsewidth;
    degree_of_rotation = degree_of_rotation == config->max_degree ? config->max_degree : degree_of_rotation % config->max_degree;
    uint16_t pwm_of_degree = ((config->max_pulsewidth - config->min_pulsewidth) * degree_of_rotation) / config->max_degree;

    if (config->direction > 0)
    {
        cal_pulsewidth = is_reverse ? config->min_pulsewidth + pwm_of_degree : config->max_pulsewidth - pwm_of_degree;
    }
    else
    {
        cal_pulsewidth = is_reverse ? config->max_pulsewidth - pwm_of_degree : config->min_pulsewidth + pwm_of_degree;
    }

    return cal_pulsewidth;
}

uint16_t servo_ease_cal(ease_config_t *ease_config, servo_status_t *status)
{
    uint16_t easing_pulsewidth = 0;
    
    if (status->last_pulsewidth <= status->currtent_pulsewidth) {
        easing_pulsewidth = status->last_pulsewidth + easeing(ease_config->ease_out, status->step_positon, 0, status->currtent_pulsewidth - status->last_pulsewidth, status->step_to);
    } else {
        easing_pulsewidth = status->last_pulsewidth - easeing(ease_config->ease_out, status->step_positon, 0, status->last_pulsewidth - status->currtent_pulsewidth, status->step_to);
    }

    if (++status->step_positon >= status->step_to || abs(status->last_pulsewidth - status->currtent_pulsewidth) < 20) {
        status->is_easing = false;
    }

    return easing_pulsewidth;
}

uint16_t servo_get_degree(servo_status_t *status)
{
    return status->currtent_degree;
}

uint16_t servo_get_course_to_degree(servo_t *servo)
{
    uint16_t deg = servo->internal.pan.currtent_degree < servo->internal.course ? servo->internal.pan.currtent_degree + 360u : servo->internal.pan.currtent_degree;
    return deg - servo->internal.course;
}

uint32_t servo_get_pulsewidth(servo_status_t *status)
{
    return status->last_pulsewidth;
}

uint32_t servo_get_easing_sleep(servo_status_t *status)
{
    return status->step_sleep_ms;
}
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

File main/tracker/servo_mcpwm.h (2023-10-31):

#pragma once

#include "target/target.h"

#if defined(ESP32) && defined(USE_MCPWM)
#include <stdint.h>

#include "driver/mcpwm.h"
#include "soc/mcpwm_reg.h"
#include "soc/mcpwm_struct.h"

#include "util/time.h"
#include "util/ease.h"

#define SERVO_MCPWM_FREQUENCY 50

#define SERVO_MCPWM_UNIT MCPWM_UNIT_0
#define SERVO_MCPWM_TIMER MCPWM_TIMER_0
#define SERVO_MCPWM_DUTY_MODE MCPWM_DUTY_MODE_0
#define SERVO_MCPWM_COUNTER_MODE MCPWM_UP_COUNTER

#define SERVO_PAN_MCPWM_IO_SIGNALS MCPWM0A
#define SERVO_TILT_MCPWM_IO_SIGNALS MCPWM0B

#define SERVO_PAN_MCPWM_OPR MCPWM_OPR_A
#define SERVO_TILT_MCPWM_OPR MCPWM_OPR_B

typedef struct _Notifier notifier_t;

typedef struct servo_mcpwm_config_s
{
    //gpio
    uint8_t gpio;

    uint16_t min_pulsewidth;
    uint16_t max_pulsewidth;
    uint16_t max_degree;
    uint16_t min_degree;
    uint8_t direction;
} servo_mcpwm_config_t;

typedef struct servo_mcpwm_status_s
{
    uint16_t currtent_degree;
    uint16_t currtent_pulsewidth;
    uint16_t last_pulsewidth;
    uint16_t ease_start_pulsewidth;
    time_millis_t next_tick;

    uint16_t step_positon;
    uint16_t step_to;
    uint32_t step_sleep_ms;
    bool is_easing;
    bool is_reverse;

    servo_mcpwm_config_t config;

    uint16_t (*pTr_pulsewidth_cal)(servo_mcpwm_config_t *config, uint16_t degree_of_rotation, bool is_reverse);
} servo_mcpwm_status_t;

typedef struct servo_mcpwm_s
{
    bool is_reversing;

    struct 
    {
        uint16_t course;
        
        servo_mcpwm_status_t pan;
        servo_mcpwm_status_t tilt;

        ease_config_t ease_config;
        notifier_t *reverse_notifier;
    } internal;
} servo_mcpwm_t;

void servo_pwm_initialize(servo_mcpwm_t *servo);
void servo_pwm_configuration(servo_mcpwm_status_t *servo, hal_gpio_t gpio);
void servo_pwm_out(servo_mcpwm_status_t *status, uint16_t pulsewidth);
#endif

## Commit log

2019-03-07 Add base code.
    [partitions.csv]
2019-03-08 copy some code from RAVEN and Test servo run is done.
    [partitions.csv]
2019-03-13 test servo and test screen
2019-03-14 Main screen and battery voltage masurement
2019-03-16 Add PCB schematic diagram and layout.
2019-03-19 LED color gradient when tracking
2019-03-29 Add kalman filter for battery value measure
2019-04-09 Pulsewidth control is abstracted to support MCPWM and LEDC
2019-04-26 Fix pcb bugs and add pcb bom
    [BOM_iAts_Pro.csv]
2019-04-30 Move servo func to tracker folder.
2019-05-06 button switch wifi smart config and connect
2019-05-13 Battery box width and height add parentheses
2019-05-13 modify reversing led status
2019-05-13 Make the servo move smoothness.
2019-05-13 add servo settings.
2019-05-13 add default step delay millis.
2019-05-15 Modify button functions.
2019-05-17 add tilt reverse icon.
    [logo.h]
2019-05-17 add seted led mode.
2019-05-20 Optimize button operation functions.
2019-05-22 Add battery settings.
2019-05-22 Optimize some functions。
2019-06-02 Modify led effect.
2019-08-08 modify power monitoring
2019-08-16 battery setting add vlotage
2019-08-16 add new spi function
2019-09-03 cut code
2019-09-08 Abstract the uart.
2019-09-14 Beeper and led flash when "COURSE" seted.
2019-12-25 Add Pelco_d protocol for uart output.
2020-02-17 Get ground speed via mavlink
2020-02-17 Refactor i2c prot
2020-05-25 Add 9250 i2c driver.
2020-05-25 Add function for Board V2.2.2
2020-05-25 Add imu settings.
2020-05-25 abstract i2c layer.
2020-05-25 mpu9250 driver.
2020-05-25 add i2c function.
2020-05-25 Add IMU related functions.
2020-05-25 add i2c_bus config.
2020-05-25 add imu settings handler.
2020-05-25 Add IMU related functions
2020-05-25 imu and i2c function.
2020-07-24 Auto switch screen I2C channel
2020-07-24 define two i2c bus
2020-07-24 debug imu function.
2020-08-10 Fix bug for auto select screen bus.
    [main.c]
2020-08-10 add imu frequency tag.
2020-08-10 debug for imu.
2020-08-10 skip secondary screen if imu disable.
2020-08-14 use home and plane object to track
2020-08-16 set calibration time to center.
2020-08-16 fix calibration acc get axis value = 0
2020-08-16 show calibration status to ui.
2020-08-16 auto home heading from imu data.
2020-09-11 upload cases stl file.
    [iAts_Pro_Antenna_holder.stl, iAts_Pro_Antenna_holder_20db_small.stl, iAts_Pro_Antenna_short_servo_holder.stl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]
2020-09-11 upload stp file.
    [iAts_Pro_Cases.stp]
2020-09-11 case readme.md
2020-09-18 add bom and gerber.
    [BOM_iAts_RX_Pro_V2.3.csv]
2020-09-28 if imu is enable and can use calibration.
2020-09-28 init mpu9250 after i2c init.
2021-01-11 fix some error.
    [iAts_Pro_Back.stl, iAts_Pro_Frame_Back.stl]
2021-01-11 add countersunk screw cases
    [iAts_Pro_Back.stl, iAts_Pro_Bottom.stl, iAts_Pro_Front_V3.stl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]
2021-01-11 add Countersunk Screw link
2021-01-14 Add Power On GPIO_LEVEL settings
2023-10-18 all doc,tools,fw,app uploaded
    [BOM_iAts_RX_Pro_V3.0.xlsx]
2023-10-31 Reconstruction the project with the directory structure of ESP-idf
    [partitions.csv]
